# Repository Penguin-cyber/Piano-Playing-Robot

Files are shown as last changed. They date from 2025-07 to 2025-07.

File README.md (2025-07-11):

# Introduction

As someone who grew up playing the piano, I sometimes wish I could learn it more easily. Specifically, sometimes it would be helpful to have a physical example of how to play specific passages, even without a teacher. Hence, I came up with this idea: an anthropomorphic, piano-playing robot. There are many interesting ways robotic hands could be helpful to pianists. Although there are methods by which the piano can be played autonomously, these methods do not involve anthropomorphism.

Anthropomorphic robotic hands would provide an accurate reference that pianists
could use when learning various pieces. They would provide excellent utility for pianists
who wish to understand the technique and form required for challenging passages. Thus,
it serves as a powerful tool to accelerate piano mastery.

Another point is that anthropomorphic robotic hands could serve as a remote means for individuals to connect with each other. Even in isolation, pianists would be able to connect with others, potentially teleoperating the robotic hand to play with others. Moreover, this teleoperation could potentially be saved locally on the arm itself, enabling the widespread education and demonstration of how certain pieces may be played.

*Importantly, this project does not intend to replace human pianists. It simply serves as an aid for them to improve and dive deeper into their craft.*

The robot has an arm with 2 degrees of freedom (DOF), which rests on a rail with one DOF. Moreover, the hand itself has 10 DOF—that is, 2 DOF per finger, enabling each finger to yaw and pitch. In total, the system has 13 DOF, requiring 13 servo motors for actuation.

# Images





## Hand



## Forearm




## Base Arm






## Linear Slide






## Custom JST adapter board




# Wiring Diagram



# Bill of Materials
| PART	| QTY. |
| --- | --- |
| 608 - 2RS Bearing| 28|
|3mm OD x 18mm pin|39|
|FeeTech Servo SCS15|3|
|50-37-5033|35|
|JST Adapter Board_PCB|5|
|Zeee 2S 5200mAh Lipo Battery 7.4V 50C	|1|
|LiPo 2S-3S Battery Balancer Charger|	1|
|FeeTech Servo SCS0009|	10|
|FE-URT-1|2|
|linear guide WS-10-40	|1|
|linear guide bearing WJ200UM-01-10	|4|
|PTFE Tubing	|1|
|Piscifun Lunker Braided Line - 40Lbs	|1|
|PLA	|4kg|

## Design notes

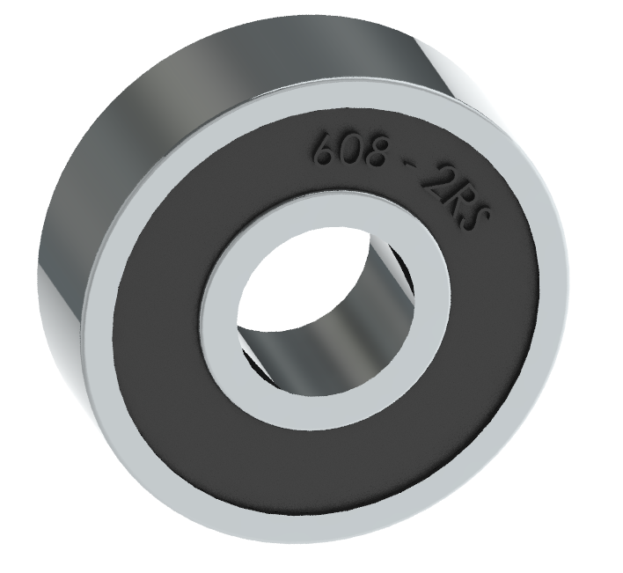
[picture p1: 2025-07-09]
COTS/608-2RS/Screenshot 2021-04-20 001353.png

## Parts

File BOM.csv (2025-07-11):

ITEM NO. | PART | QTY. | LINK
1 | 608 - 2RS Bearing | 28 | https://a.co/d/gffOpsG
2 | 3mm OD x 18mm pin | 39 | https://a.co/d/2721Kti
3 | FeeTech Servo SCS15 | 3 | https://www.alibaba.com/product-detail/Feetech-15kg-Torque-Serial-Bus-Servo_62053510385.html
4 | 50-37-5033 | 35 | https://www.mouser.ca/ProductDetail/Molex/50-37-5033?qs=AplfTeSvkkCfnVdKv8UuEg%3D%3D
5 | JST Adapter Board_PCB | 2 (min order 5) | Ordering through https://jlcpcb.com/
6 | Zeee 2S 5200mAh Lipo Battery 7.4V 50C | 1 | https://a.co/d/ivJBptk
7 | LiPo 2S-3S Battery Balancer Charger | 1 | https://a.co/d/hdVfxbw
8 | FeeTech Servo SCS0009 | 10 | https://www.alibaba.com/product-detail/Feetech-SCS0009-Pink-RX1-Servo-Assembly_1601300990382.html
9 | FE-URT-1 | 2 | https://www.alibaba.com/product-detail/Feetech-FE-URT-1-Multi-Function_1600953053272.html
10 | linear guide WS-10-40 (501mm) | 1 | https://www.igus.ca/product?artNr=WS-10-40
11 | linear guide bearing WJ200UM-01-10 | 4 | https://www.igus.ca/product?artNr=WJ200UM-01-10
12 | PTFE Tubing | 1 | https://a.co/d/8Bh5Cs5
13 | Piscifun Lunker Braided Line - 80Lbs | 1 | https://a.co/d/38KP9f7
14 | PLA | 4kg | https://a.co/d/aLZwPXa

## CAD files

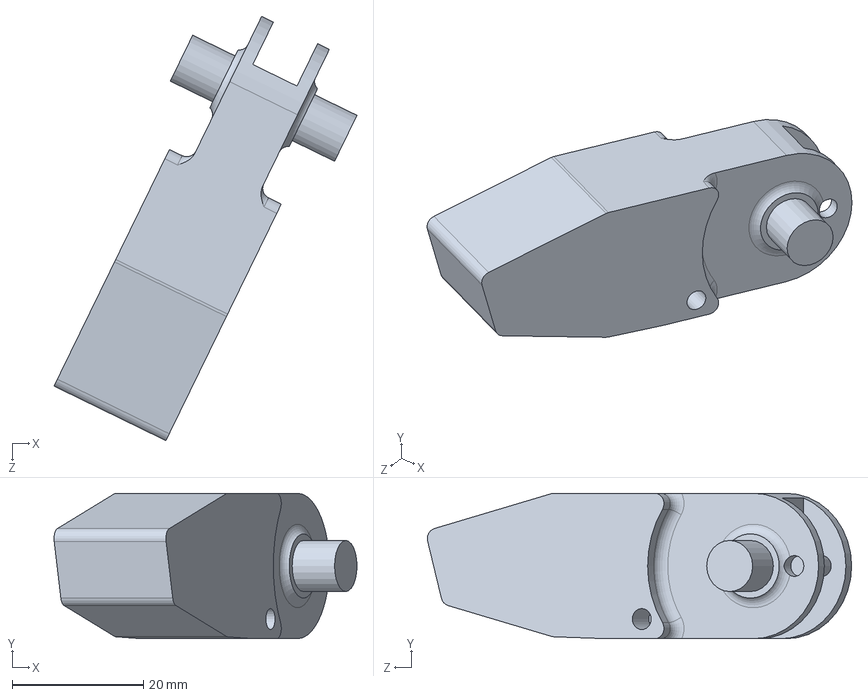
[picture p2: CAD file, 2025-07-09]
CAD Files/hand/fingers/pinky/pinky distal.SLDPRT
46.2 x 22.2 x 64.8 mm

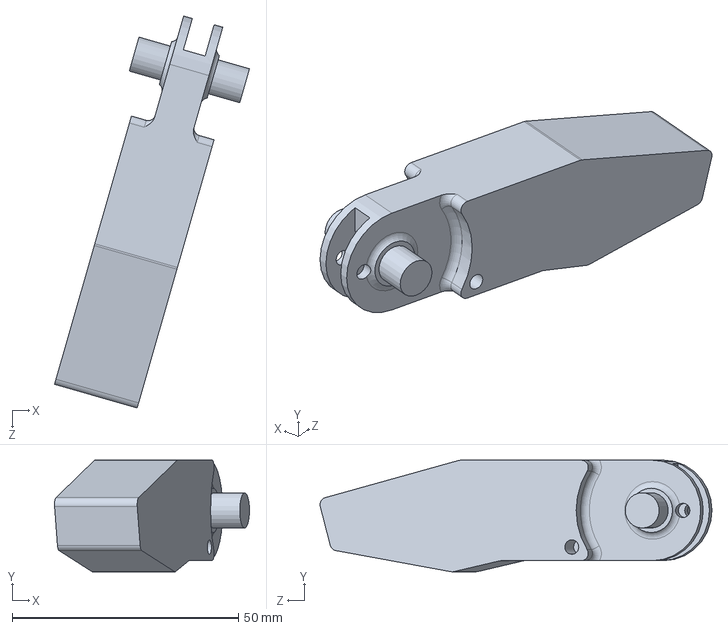
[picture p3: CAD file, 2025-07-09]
CAD Files/hand/fingers/ring/ring distal.SLDPRT
43.1 x 24.7 x 86.6 mm

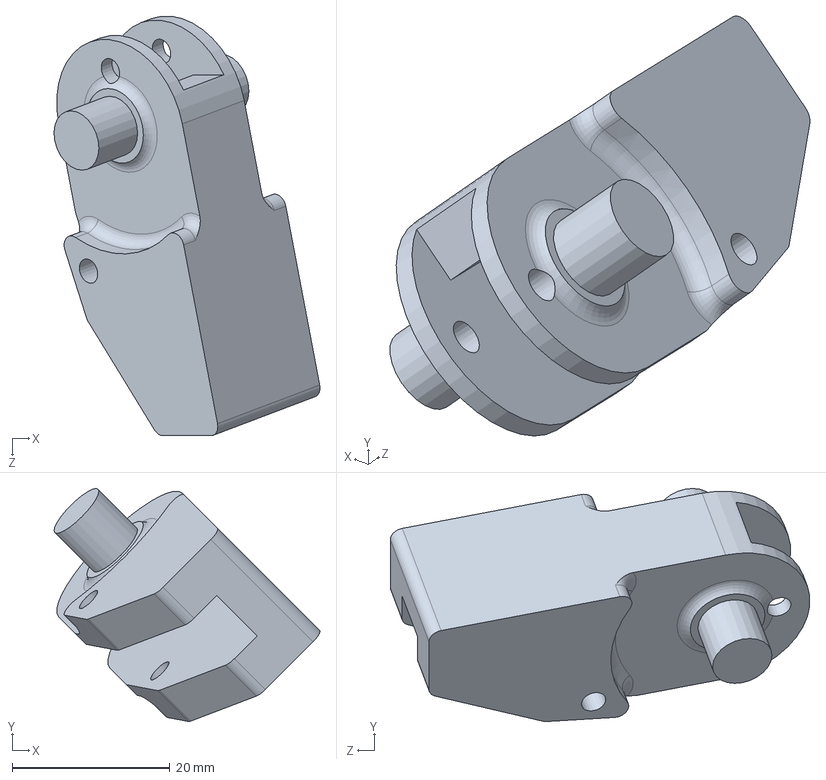
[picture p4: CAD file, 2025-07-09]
CAD Files/hand/fingers/thumb/thumb distal.SLDPRT
33.8 x 29.6 x 53.3 mm

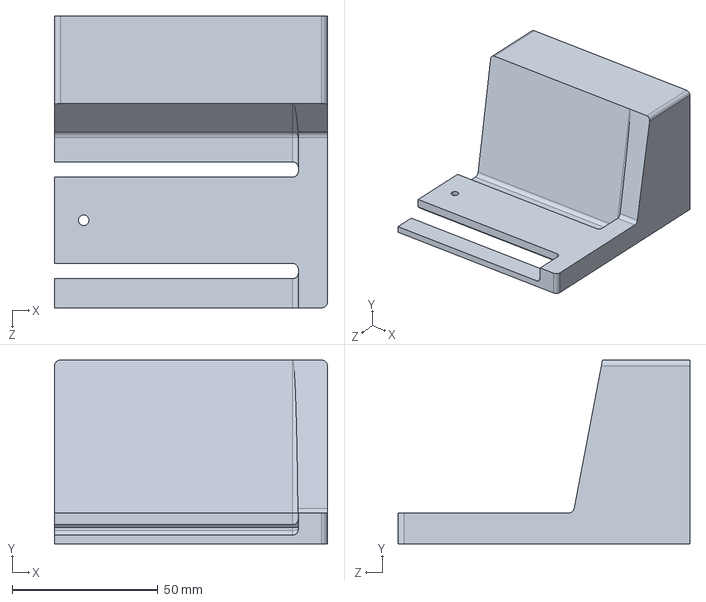
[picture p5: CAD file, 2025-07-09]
CAD Files/rail ends/Mirrorbase rail end.SLDPRT
93.7 x 63.1 x 100.1 mm

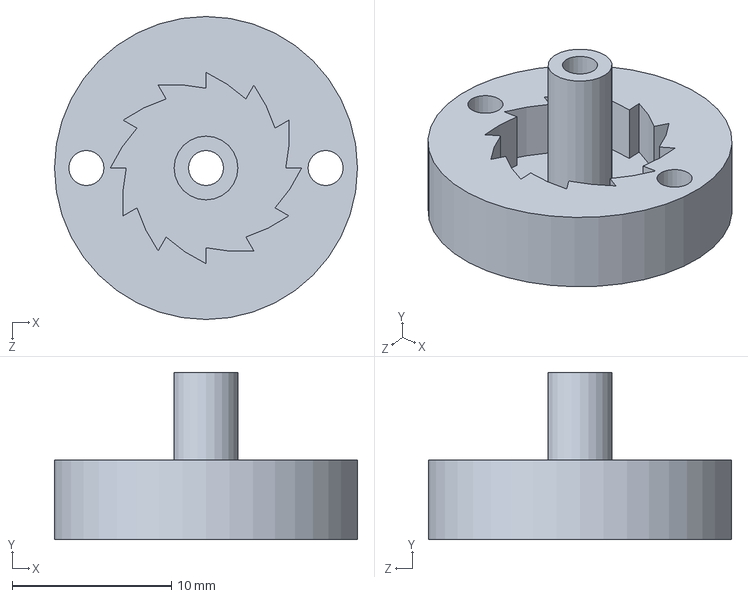
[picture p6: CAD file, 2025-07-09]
CAD Files/ratcheting pulley/bottom half.SLDPRT
19.0 x 10.5 x 19.0 mm

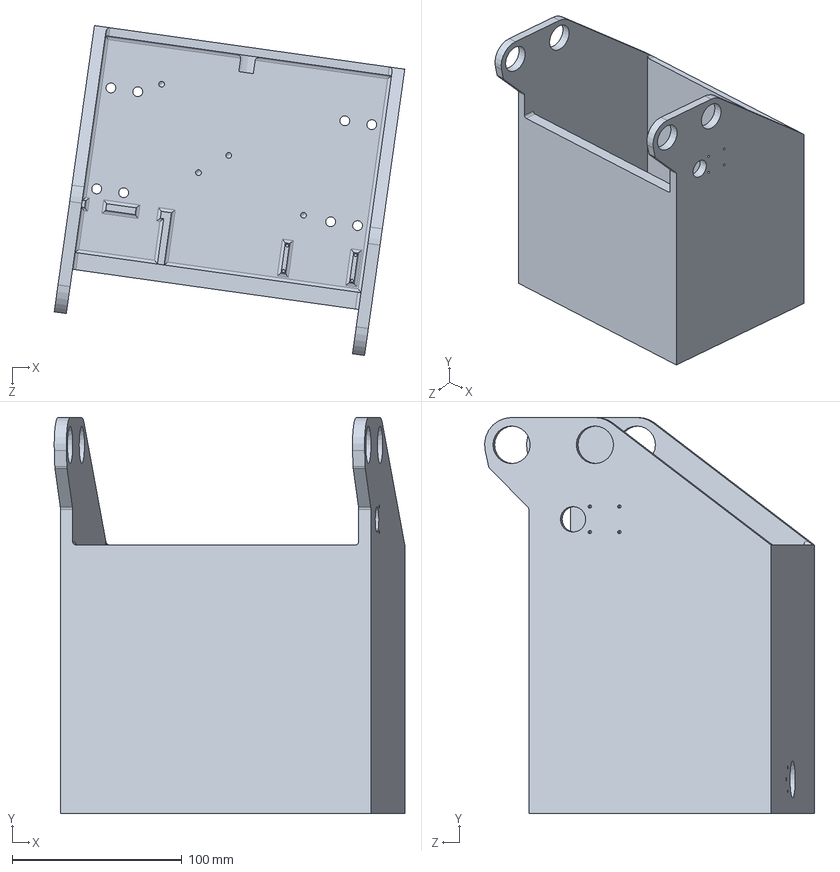
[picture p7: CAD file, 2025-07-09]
CAD Files/base arm/base arm.SLDPRT
206.3 x 233.0 x 194.1 mm

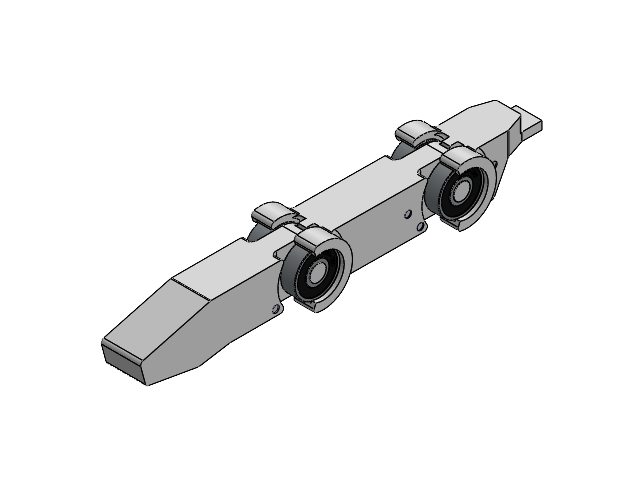
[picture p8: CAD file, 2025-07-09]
CAD Files/hand/fingers/middle/middle assembly.SLDASM
middle distal
middle proximal
finger joint
608 - 2RS x 4
3mm OD x 18mm pin x 6
3mm OD x 9mm pin x 2

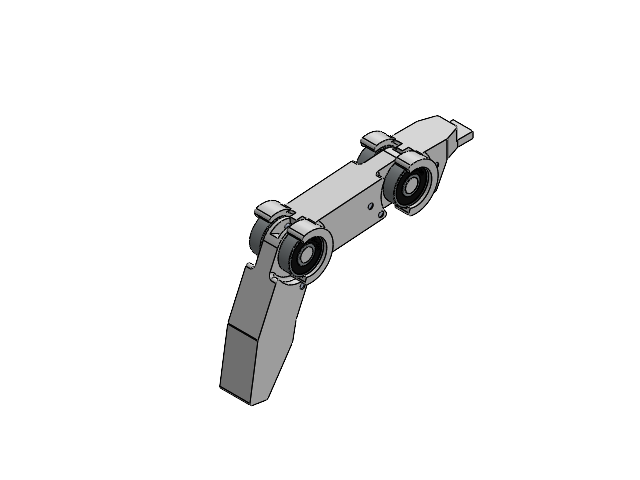
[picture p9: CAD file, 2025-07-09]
CAD Files/hand/fingers/ring/ring assembly.SLDASM
ring distal
ring proximal
finger joint
608 - 2RS x 4
3mm OD x 18mm pin x 6
3mm OD x 9mm pin x 2

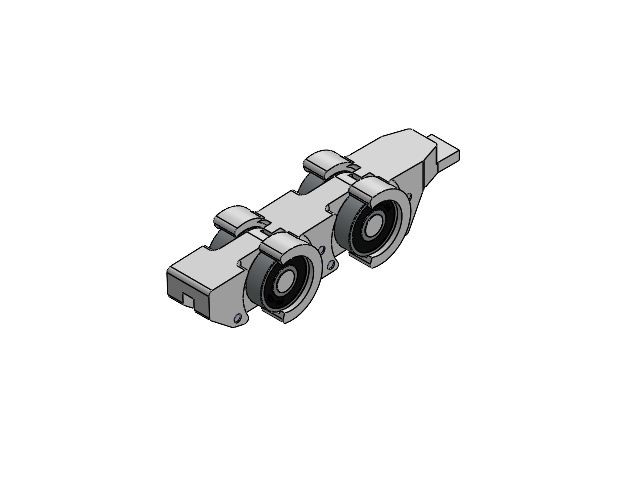
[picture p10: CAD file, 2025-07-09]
CAD Files/hand/fingers/thumb/thumb assembly.SLDASM
finger joint
thumb proximal
thumb distal
608 - 2RS x 4
3mm OD x 18mm pin x 6
3mm OD x 9mm pin x 2

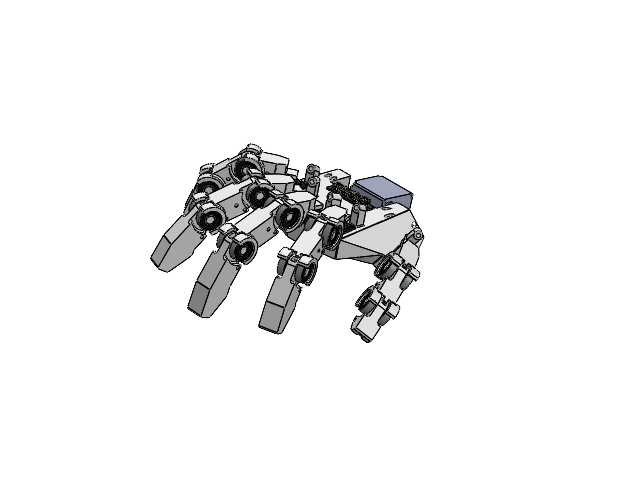
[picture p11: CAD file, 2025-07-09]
CAD Files/hand/hand assembly.SLDASM
palm
finger joint x 5
thumb proximal
thumb distal
608 - 2RS x 20
3mm OD x 18mm pin x 30
3mm OD x 9mm pin x 9
91772A071_NO THREADS_Passivated 18-8 Stainless Steel Pan Head Phillips Screw x 20
eBom-FreeParts x 5
Servo SC15
index distal
index proximal
middle distal
middle proximal
ring distal
ring proximal
pinky proximal
pinky distal
JST_EH_B3B-EH-A_1x03_P2.50mm_Vertical.step x 7
JST Adapter Board_PCB.step

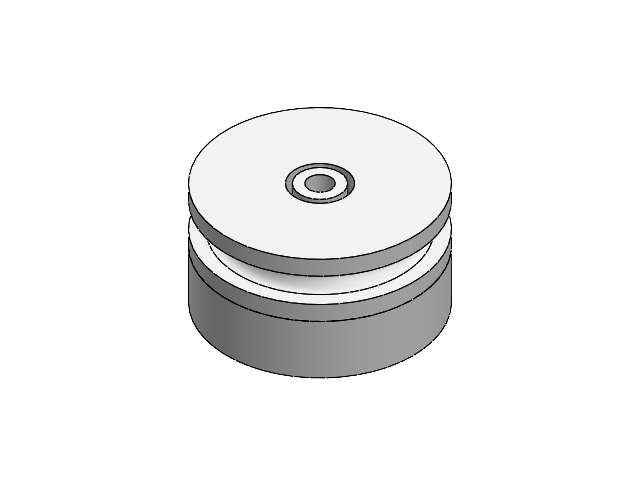
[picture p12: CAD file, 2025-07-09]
CAD Files/ratcheting pulley/ratcheting pulley.SLDASM
bottom half
top half

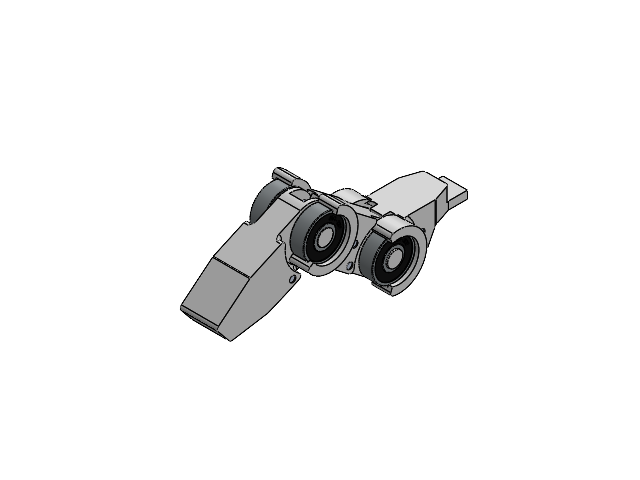
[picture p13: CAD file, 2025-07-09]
CAD Files/hand/fingers/pinky/pinky assembly.SLDASM
pinky proximal
pinky distal
finger joint
608 - 2RS x 4
3mm OD x 18mm pin x 6
3mm OD x 9mm pin x 2

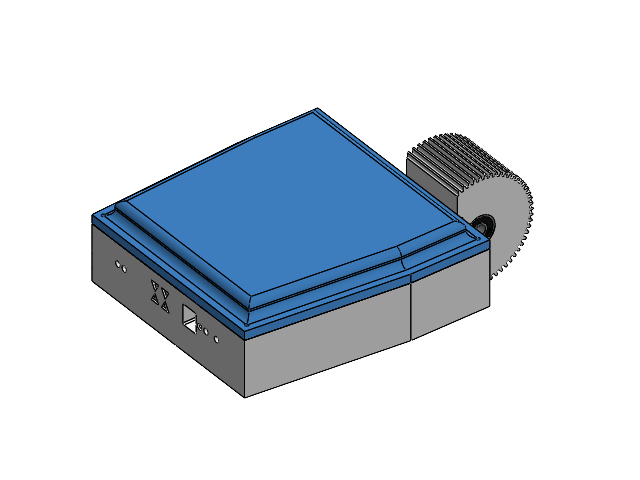
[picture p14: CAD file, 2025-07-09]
CAD Files/forearm/forearm assembly.SLDASM
forearm top half
forearm bottom half
91772A071_NO THREADS_Passivated 18-8 Stainless Steel Pan Head Phillips Screw x 20
eBom-FreeParts x 5
bottom half x 5
top half x 5
JST_EH_B3B-EH-A_1x03_P2.50mm_Vertical.step x 7
JST Adapter Board_PCB.step
608 - 2RS x 2
20DP 60T gear with mount

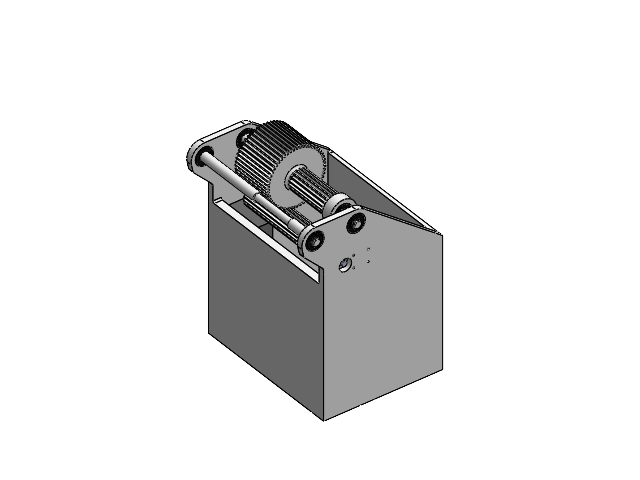
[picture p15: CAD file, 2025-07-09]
CAD Files/base arm/base arm assembly.SLDASM
base arm
Servo SC15 x 2
CX90B-16P_3D
Thermal_Shape
Nano ESP32 PCB 1.26.1
Nano ESP32 PCB 1.26.2
Nano ESP32 PCB 1.26.3
Nano ESP32 PCB 1.26.4
Nano ESP32 PCB 1.26.5
Nano ESP32 PCB 1.26.6
Nano ESP32 PCB 1.26.7
Nano ESP32 PCB 1.26.8
Nano ESP32 PCB 1.26.9
Nano ESP32 PCB 1.26.10
Nano ESP32 PCB 1.26.11
Nano ESP32 PCB 1.26.12
Nano ESP32 PCB 1.26.13
Nano ESP32 PCB 1.26.14
Nano ESP32 PCB 1.26.15
Nano ESP32 PCB 1.26.16
Nano ESP32 PCB 1.26.17
Nano ESP32 PCB 1.26.18
Nano ESP32 PCB 1.26.19
Nano ESP32 PCB 1.26.20
Nano ESP32 PCB 1.26.21
Nano ESP32 PCB 1.26.22
Nano ESP32 PCB 1.26.23
Nano ESP32 PCB 1.26.24
Nano ESP32 PCB 1.26.25
Nano ESP32 PCB 1.26.26
Nano ESP32 PCB 1.26.27
Nano ESP32 PCB 1.26.28
Nano ESP32 PCB 1.26.29
Nano ESP32 PCB 1.26.30
Nano ESP32 PCB 1.26.31
Nano ESP32 PCB 1.26.32
Nano ESP32 PCB 1.26.33
Nano ESP32 PCB 1.37.1
kicad_embedded_8E73D9F8F36F4F9977290BE86F45DC9F x 4
kicad_embedded_45DA18D544D879B7BDBAFA8977EECF00 x 21
kicad_embedded_DEF0F92913685E26D857FD1FB7A2F78D x 5
kicad_embedded_C98002EB64DF73D5E591C0EAEEF6F48A
kicad_embedded_4DDFC06D8070CBA906BE37562F7B494A x 2
kicad_embedded_999C82AB9CC9DBED1893E338DD6C2316
kicad_embedded_ADBE63E95B39FBFA0098FDD834B68290 x 4
kicad_embedded_F9954E0880D22F307436BA6318327092 x 6
kicad_embedded_5625576866E5ED7B8B38EA378BFE11EE
kicad_embedded_B5AE8CB27AD4C08C78F0F2DF715B6909 x 2
kicad_embedded_E5EC1D9E140243425E0A49AB96938633
kicad_embedded_45744145A6B1DC0DD3C09A460432275A
PCB_PCB
Zeee 2S 5200mAh Lipo Battery 7.4V 50C
intermediary gear
608 - 2RS x 6
SCS15 servo horn x 2
first stage servo pinion
intermediary stage large spacer
intermediary stage small spacer
second stage large spacer
second stage small spacer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

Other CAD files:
CAD Files/hand/fingers/index/index assembly.SLDASM
CAD Files/base arm/base arm mastermodel.SLDPRT
CAD Files/forearm/forearm mastermodel.SLDPRT
CAD Files/hand/hand mastermodel.SLDPRT
CAD Files/base arm/double pulley.SLDPRT
CAD Files/base arm/first stage servo pinion.SLDPRT
CAD Files/base arm/intermediary gear.SLDPRT
CAD Files/base arm/intermediary stage large spacer.SLDPRT
CAD Files/base arm/intermediary stage small spacer.SLDPRT
CAD Files/base arm/second stage large spacer.SLDPRT
CAD Files/base arm/second stage small spacer.SLDPRT
CAD Files/base arm/shaft.SLDPRT
CAD Files/forearm/20DP 60T gear with mount.SLDPRT
CAD Files/forearm/forearm bottom half.SLDPRT
CAD Files/forearm/forearm top half.SLDPRT
CAD Files/hand/finger joint.SLDPRT
CAD Files/hand/fingers/index/index distal.SLDPRT
CAD Files/hand/fingers/index/index proximal.SLDPRT
CAD Files/hand/fingers/middle/middle distal.SLDPRT
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

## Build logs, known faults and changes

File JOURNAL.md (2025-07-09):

---
Title: Anthropomorphic, Piano-Playing Robot
Author: MengYang Yu
Description: A robot that plays the piano using an anthropomorphic robotic hand.
Created_at: 2025-06-08
Total_Time: 63 hours
---
# June 8: Started designing the forearm

Today, I worked on drafting ideas for what the entire arm system might look like. This was done on a separate Google Doc: https://docs.google.com/document/d/1JBX58aGr_KxgK6paylfiLBcvCcq8-dvwz1_QLYsHlvY/edit?usp=sharing in the "Arm Decisions" Tab. The primary concern was on how the hand would access the keys in various ranges on the piano. Ultimately, I settled on doing a rail system, due to its simplicity. 

Otherwise, I began CADing the forearm in SolidWorks. I have general ideas for the servo motors and a concept in mind of what it may end up looking like. I am still figuring out where to place the ESP32 and the corresponding control boards for the serial communication. 

For packaging purposes, I may have to design a PCB that combines six serial ports in parallel, just so I don’t have to use the boards that come with the servos, which are pretty space inefficient since they only combine two ports.



**Time spent: 2h**

# June 10: Started designing the PCB

Today, I worked on a custom PCB to connect the six serial bus ports in parallel. I have used KiCAD before, but I'm a little rusty, so a lot of the time spent was trying to relearn the basics of KiCAD. I created the project, drew the schematic, and started working on the PCB layout. In previous projects, I would accidentally make the PCB too large; accordingly, I chose to focus on space this time to ensure that the board would not be too expensive, and that it would actually be more space efficient than the boards that come with the servos. For mounting purposes, I added some holes where M2 bolts can go.



**Time spent: 1:30h**

# June 11: Finished the PCB & further planning for arm

Today, I worked on finishing the PCB. Again, I aimed to optimize the size of the board, since that was the primary motivation for designing it in the first place. I managed to get the board down to 11mm x 49.5mm, which, in my opinion, is a good size. After finishing up everything (which took a while because I was relearning some more KiCad stuff), I started drafting ideas for how to actuate the pivot. I came to the conclusion that the pivot should be a dead axle which has a tooth profile on the outside. This way I can drive it with precision, and this would work especially well since the range of motion is rather limited, ~45 degrees.




**Time spent: 2:30h**

# June 16: Finished drafting the profiles of the arm & started designing the pulley

Today, I worked on the profiles of the arm. I have the layout complete now, and all that is left is to actually make the parts for the arm. I will add mounting holes onto the outside flange and I may change the height of the arm. I also started designing a ratcheting pulley, which would be incredibly useful. I have the general design for it finished, and simply need to start cadding it. Again, all of the logic and main decision-making is outlined in my document on the Google Drive. The majority of the time was spent on drafting and thinking, and not so much on actual cad.



**Time spent: 2h**

# June 17: Cadding pulley

Today, I worked on cadding the pulley. I mapped out the mastermodel for the pulley, and all that is left is to extrude the pieces. I have already extruded and made the bottom piece, only the top remains. After this is done, I will extrude parts on the arm to create the arm. Most of the time spent today was on figuring out the precise placement of features within the pulley. This was primarily deciding on tolerances and clearances, as well as figuring out what the ratchet profile should look like.




**Time spent: 2h**

# June 18: Cadding pulley cont. and tendons

Today, I finished cadding the pulley by extruding the top half and creating the assembly. After finishing, I pulled those dimensions into the main mastermodel for the forearm, defining the desired height of the arm to encase the pulleys. After doing so, I created a block for the servo with the pulley, to help me map out the tendons. The tendons were then routed, with the supporting structure created. I will work on extruding the parts of the arm, and putting finishing touches on the design. There were no major design decisions made today, just simple tolerancing and clearances.





**Time spent: 5h**

# June 19: Cadding forearm

Today, I extruded the parts of the arm and refined a bit of the design. Naturally, as things are extruded and designed, small adjustments are made where things don't work exactly as envisioned. For example, I tweeked the general shape of the forearm such that the holes for the PTFE lined up correctly. The tendons' paths were updated to ensure that the holes pierced the correct sections. The assembly for the forearm will be completed next.




**Time spent: 4h**

# June 20: Creating forearm assembly and main assembly

Today, I created the assemblies for the forearm and the main assembly. This was primarily to set up the calculations I will do tomorrow to determine the reduction necessary in my gearbox. I also created a PLA material in SolidWorks to better match real life, so my math is more accurate. 




**Time spent: 2h**

# June 21: Designing the pivot gearbox

Today, I created the ratios for the pivot gearbox

After running some calculations based on SolidWorks’s data, I was able to calculate the torque required to pivot the arm. The calculations are shown below. Notably, I included a safety factor (x2) to ensure that nothing breaks–I would rather have a slower arm than an arm that cannot pivot. This is possible because the pivot is not required to have an extensive range of motion; so long as it operates within its range of motion at a reasonable speed, it will suffice.

Ultimately, I decided on a two-stage gearbox: 18T:54T (1:3) stage and an 18T:60T (3:10) stage. The relatively similar reductions ensure that the gears experience wear equally and that the packaging is optimized (since the gears are of similar sizes).

After adding a 20DP 60T gear to the arm (at 100% infill), the mass increased, and the center of mass (COM) distance from the pivot decreased. Ultimately, the new required torque stayed within the safety tolerance I had set.

Based on my experience, I ensured that I used the rated torque and moving torque of the servo motor. This will mitigate any substantial wear or damage to the servos.



**Time spent: 4h**

# June 23: Base arm and linear slide actuation

Today, I looked at how I might actuate the lateral movement of the arm and generally how the base of the arm might look. I think I will go with a linear slide in tandem with a pulley system. This is documented on my document, but essentially it involves a spool on a servo that is connected to two sets of string. Both strings will have enough length to span the linear slide, and when the servo turns in one direction, the strings will spool or despool correspondingly, pulling the chassis to the respective ends of the slide. I will flesh this out further after adding the arm, since a gearbox may need to be included depending on the torque required.



**Time spent: 4h**

# June 24: Gearbox and base arm cad

Today, sketched out what the gearbox may look like. I made sure to include areas for bearings and mounting since it's pretty easy to forget those. I also ensured that there was no interference between stages.

Another thing I tackled was the general layout of the control boards. namely the FE-URT-1 and NANO ESP32 boards that will be used.

Furthermore, I dealt with holes for wiring, which I may update to include areas for zipties, since the wires may be passing through the gearbox. The last thing I want is to have the wires stuck on the gears and just destroyed, so I may just do that. Most of the work today was just on cadding and specifying areas.

An area I struggled with was the gearbox. Since I decided on using dead axles for the gearbox, I would need to put the gears on bearings; however, this would cause an interference problem with the gears. Hence I decided to include spacers and widen the base of the arm to match the new spacing.



**Time spent: 6h**

# June 27: Power considerations and base arm changes

Today, I started thinking more about the power.

According to my current configuration, the power consumption will resemble this.



All of the data for the table was collected from datasheets. The current ratings of the servo motors were specified in terms of the rated current, as the torque calculations were based on the rated torque.

Since the total typical current is expected to be 6700 mA–6400 mA for the servos alone, I will add FE-URT-1. This is because the screw terminals on the FE-URT-1 have a maximum current rating of 6A. Hence, I will separate the SCS0009 servos and the SCS15 servos into two different FE-URT-1 boards. These will be powered by the same power source in parallel and connect to the Nano ESP32 board’s RX and TX in parallel.

Since some RC cars are commonly powered by the cumulative voltage range (6 - 7.4V), I will be using a 2S LiPo battery. These batteries are rated at 7.4 volts and are rechargeable, making them compatible with my purposes. Ideally, the battery would last for about an hour, meaning it would need a capacity of about 6700mAh. Moreover, it would be able to safely and continuously discharge 18 600 mA (18.6 A).

As such, the battery I have chosen is Zeee 2S 5200mAh Lipo Battery 7.4V 50C. Its capacity is approximately 46 minutes (at the rated current), and it can supply a maximum of 260 A, well above the peak current of the circuit.

These changes were reflected in the base arm sketches.



**Time spent: 3h**

# June 29: Extrusion and changes

Today, I started extruding parts of the base arm, which will help me when determining the strength of my linear slide.

As I was extruding, many problems came to light. For example, I realized that I had not really thought about the mounting of the various boards and motors. Hence, a lot of time was spent on figuring that out.




While extruding the gears, I realized that it would be almost impossible to 3D-print, meaning I had to redesign the gear so that it would be easily printed. To fix it, I had to reconsider the ordering of the gears, and ultimately settled on an assymetrical design, with the gear stages distinct and separate, as opposed to a "sandwich." 

Another thing I had to figure out was how to incorporate a bearing on the side with the smaller gear, which on its own would be unable to hold a bearing. Hence, I designed an extra spacer section that would be able to house the bearing, ensuring greater stability for the gear.



**Time spent: 7h**

# July 3: Finishing assembly and updating main assembly

I worked on the assembly, making sure that I have the mass of the entire system before deciding on the rail and actuation of the rail. I created custom parts in Solidworks to ensure that all the masses are accurate, like the FE-URT-1 control board, or the LiPo battery. 




I also made the 60T gear a separate part that can be attached by bolts. This way, the forearm’s printing will be far easier and stronger.



**Time spent: 6h**

# July 4: Determining slide and pulley size

For my purposes, I will be purchasing a linear slide from igus. This is because they provide a CAD file for the linear slide I chose, which will be incredibly useful. Moreover, their slides are easily configurable according to my requirements using their digital configuration tool: https://drylin-linear-guide-expert.igus.tools/requirements?l=en&c=CA.

While my initial requirements involved being able to play keys within a range of two octaves, igus does not sell a linear slide of that length (330mm). Hence, I will opt instead for a linear slide that enables the system to play half of the keys on the keyboard; in other words, the length of the slide should be ~612.85mm. This value will be rounded down to 501mm (the minimum rail length), since the hand itself is wide enough to enable the system to play all the keys on the piano.



All of these calculations are under the assumption that an octave is approximately 165mm (which is standard for pianos).

Under the assumption that drylin® W pillow block WJ200QM-01s will be used, which have a coefficient of friction of about 0.05. With the system’s mass being 3713.42g, which will be rounded up to 8000g (approximately twice the original value), the friction force will be approximately 4N. 



Hence, with a pulley of OD 3cm, the system will reach an acceleration of approximately 3.75 ms^-2, which will be more than adequate. High acceleration is essential for this project, so I will try to keep the pulley OD as small as possible to increase the acceleration of the system.

**Time spent: 4h**

# July 7: Linear slide CAD, creating double pulley

Today I worked on the above. I added the rail and bearings into the CAD, as well as the corresponding mounting holes for the arm. With this, I created the double pulley that I will use for actuating the linear slide.




I also updated the hand CAD to utilize the board I had created, simplifying wiring.



Furthermore, I began thinking about how to design the mounting blocks for which the pulleys will hold onto. This will be a challenge since there is only one mounting hole for these end blocks, so I will have to come up with a design that is somehow rather rigid in spite of that.

**Time spent: 5h**

# July 8: Linear slide end blocks

Today, I created the end blocks on the linear slide that the pulley can attach to. I made sure that the shafts were ratcheted, meaning that I could tension the pulleys freely. This ensures that there is the correct amount of slack in the strings. Now I am done with the blocks, I am done with all of the parts.



A concern that may arise is tipping. Since the center of mass of the system is not directly above the rail (which is the system's contact point to the ground), there is a chance that the entire arm might tip over. While I find that this is unlikely, given the proximity of the COM to the rail, it is still possible. However, a simple solution may be implemented, wherein I simply tweek the design of the linear slide blocks to house weights, moving the COM closer to the rail and decreasing the likelihood of it tipping.

**Time spent: 3h**
